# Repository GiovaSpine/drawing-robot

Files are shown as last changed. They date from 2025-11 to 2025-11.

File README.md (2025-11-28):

# Drawing Robot

This project is about a 3d printed **drawing robot** I made in my first year of computer engineering in 2023, to understand in more depth how a CNC machine works.  
It was 3D modeled in *FreeCAD* and programmed for an *Arduino Uno* entirely from scratch: from the classes that control the stepper motors, to the G-code functions that draw.

It was created before I started using proper version control, and I recently decided to publish it to share my work.

---

## The Robot

**The robot** is a SCARA manipulator with three degrees of freedom, that uses nema 17 stepper motors with GT2 belts and pulleys to reach a ratio of 20:1 for the first joint and 15:1 for the second joint.  
For the last joint we have a simple rack and pinion mechanism to convert the rotation of the stepper motor into a linear motion that moves the end effector (pen) to draw or not in the drawing plane.  

The code is divided in four *Arduino* files:
- [Scara_Manipulator_V1.ino](code/arduino/Scara_Manipulator_V1.ino): it's the main file where the classes for the stepper motors and the manipulator are declared, and the manipulator object is created.
- [CNCstepperClass.ino](code/arduino/CNCstepperClass.ino): where the class for the stepper motors is defined.
- [ManipulatorClass.ino](code/arduino/ManipulatorClass.ino): where the manipulator class is defined, with its functions that use the inverse kinematics to control the robot.
- [FunzioniGCODE.ino](code/arduino/FunzioniGCODE.ino): where the G-code functions of the manipulator class are defined.  

The following files allow to visualize the robot in 3D:
- *Blender* file (created with Blender 4.5): [Scara Manipulator.blend](3D-models/Scara%20Manipulator.blend)
- *.stl* file: [Scara Manipulator.stl](3D-models/pezzi/components/Scara%20Manipulator.stl)

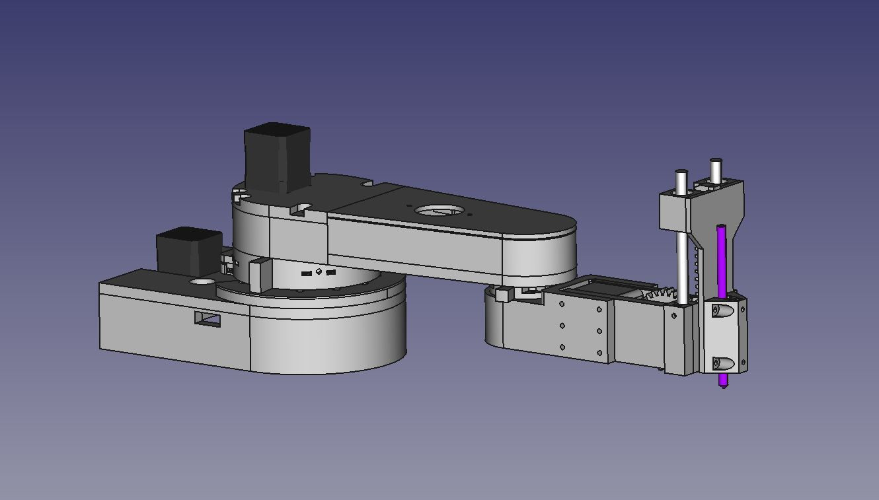
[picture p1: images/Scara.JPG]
Robot Frontale


---

## Robot in Action

The robot draws a butterfly.  

Robot in action 1

The robot draws a smiling face.  

Robot in action 3

The robot draws the letter "A".  

Robot in action 2

---

## Components
The robot was made in *FreeCAD* and designed to be able to be 3D printed in PLA with a cheap 3D printer.  
In addition we need the following components:

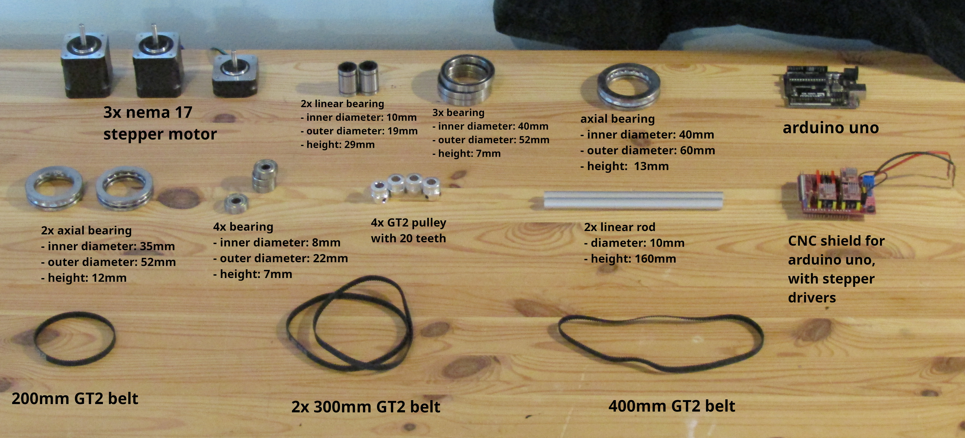
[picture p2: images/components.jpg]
Componenti Robot


---

## Robot Diagram
The robot has a very simple diagram, and in particular, since the objective is to draw, a complicated control for the $z$ axis is not needed, and so we can have two values for $z$: the value where the end effector (pen) is touching the drawing plane, and the value where it is not.  
As a result only the measurements for the horizontal links $d_2$ and $d_4$ are shown.

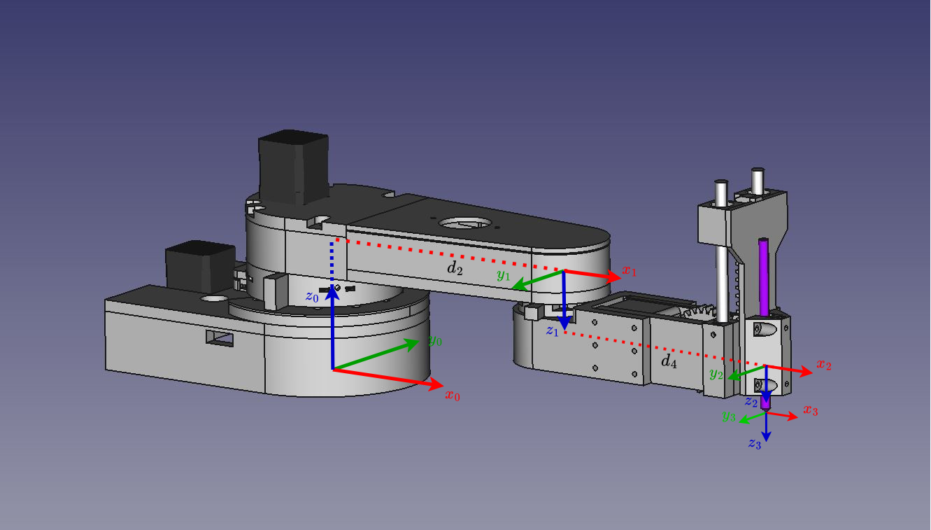
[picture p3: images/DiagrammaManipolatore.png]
Robot Diagram 1

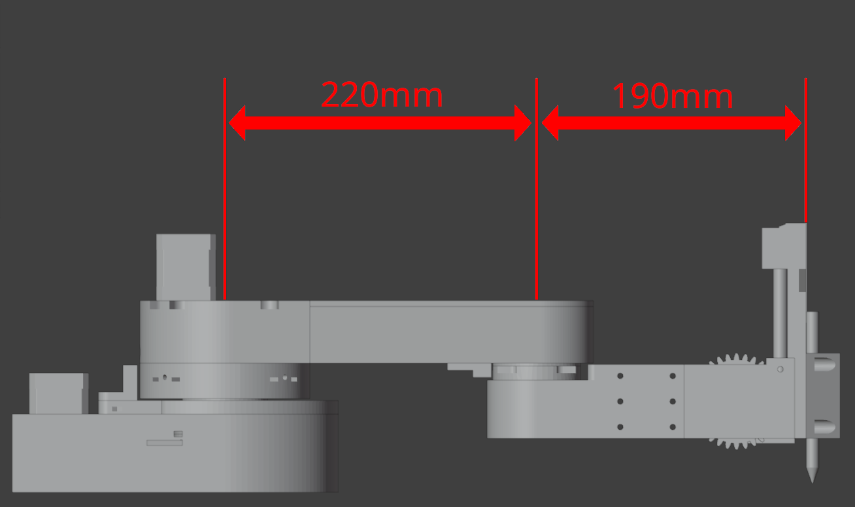
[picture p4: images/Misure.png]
Robot Diagram 2


---

## Inverse Kinematics
The **inverse kinematics** is very simple, not only because we have a three degrees of freedom manipulator, but also because with the simplification of the $z$ axis, discussed earlier, only $d_2$ and $d_4$ are used in the calculations for $\theta_1$ and $\theta_2$ (the angles of the first two joints respectively).  
For $\theta_3$ we need only to know the two values that allow the end effector (pen) to touch or not the drawing plane.

In the following image, two kinematic diagrams are shown. They represent a top view of the robot: one corresponds to a configuration where the desired $y_0$ is greater than 0, and the other where it is less than 0.
The equations derived using basic trigonometry are also included.
Inverse Kinematics

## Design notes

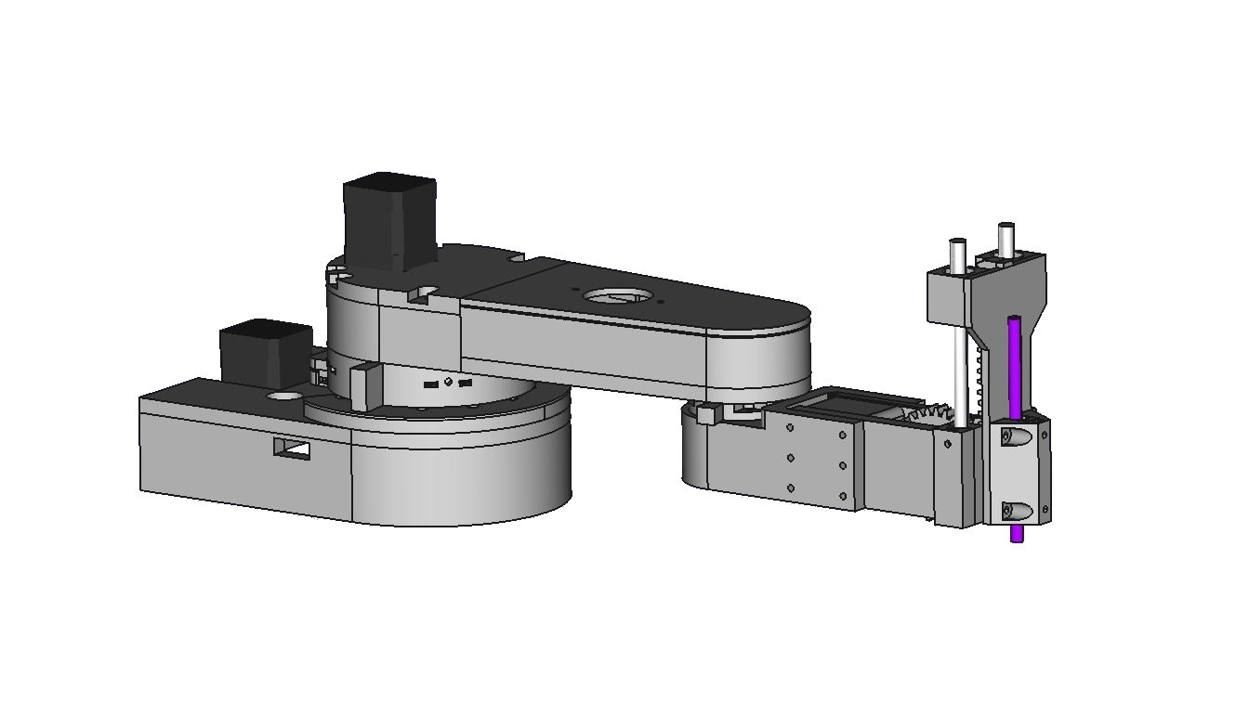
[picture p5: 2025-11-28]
images/Scara2.JPG

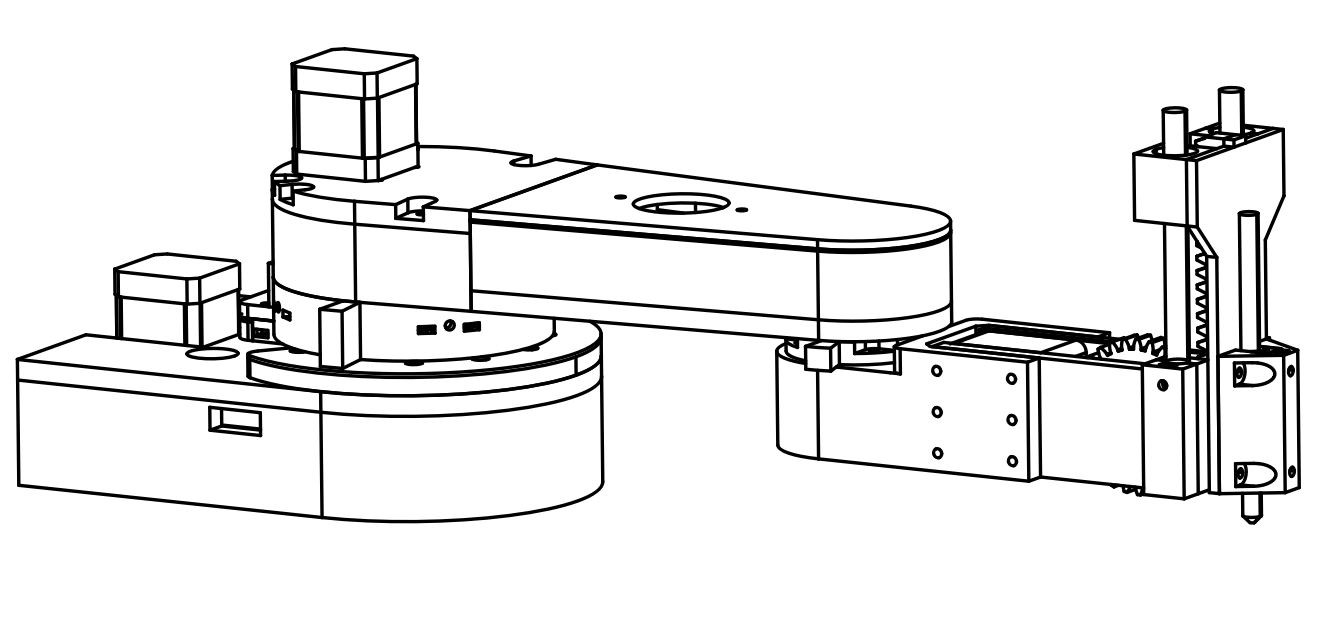
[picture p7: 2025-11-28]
images/Scara3.JPG

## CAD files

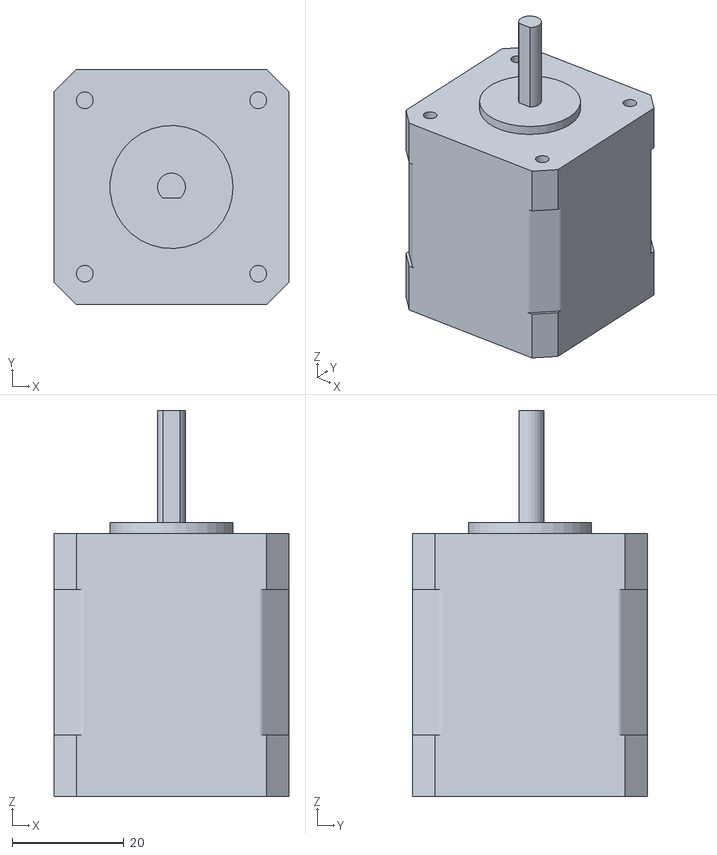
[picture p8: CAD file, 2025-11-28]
3D-models/pezzi/components/Stepper Motor-Nema 17 lenght_42.stl
42.0 x 42.0 x 69.0

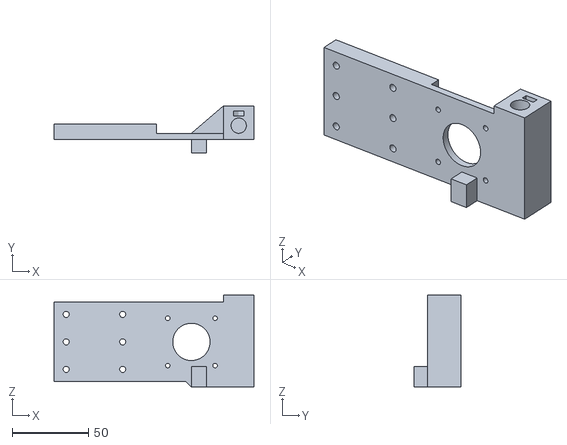
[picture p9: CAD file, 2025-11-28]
3D-models/pezzi/PJ-Base Pezzo Motore.stl
131.0 x 31.0 x 60.2

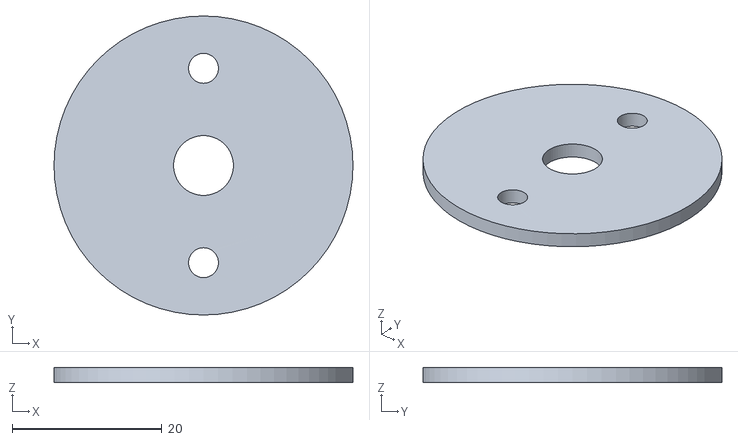
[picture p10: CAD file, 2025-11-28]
3D-models/pezzi/pulley/Coperchio Pulley 60 - Omero.stl
40.0 x 40.0 x 2.00

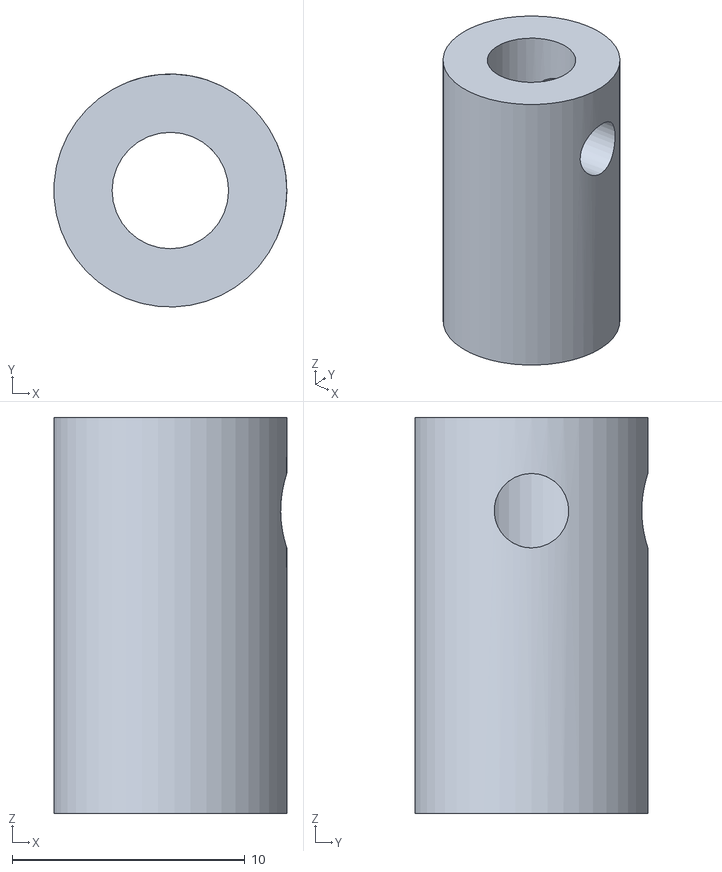
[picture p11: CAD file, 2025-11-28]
3D-models/pezzi/Albero Accopiamento Pulley-Nema 17.stl
9.99 x 10.00 x 17.0

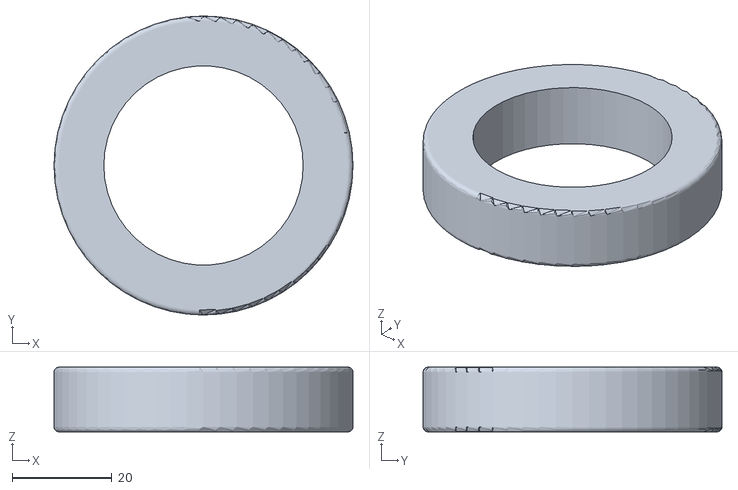
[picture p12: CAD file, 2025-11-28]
3D-models/pezzi/components/Cuscinetto assiale 40.stl
60.0 x 60.0 x 13.0

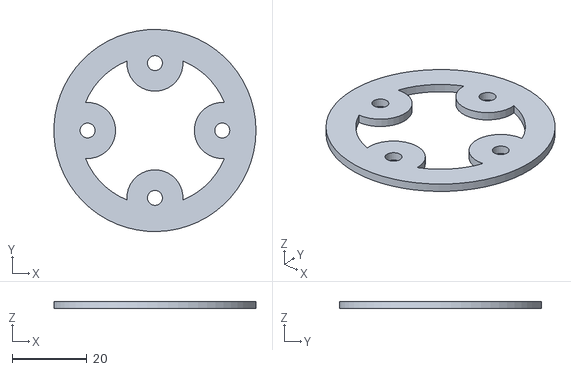
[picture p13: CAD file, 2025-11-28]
3D-models/pezzi/pulley/Coperchio Pulley 80 - Base.stl
54.0 x 54.0 x 2.00

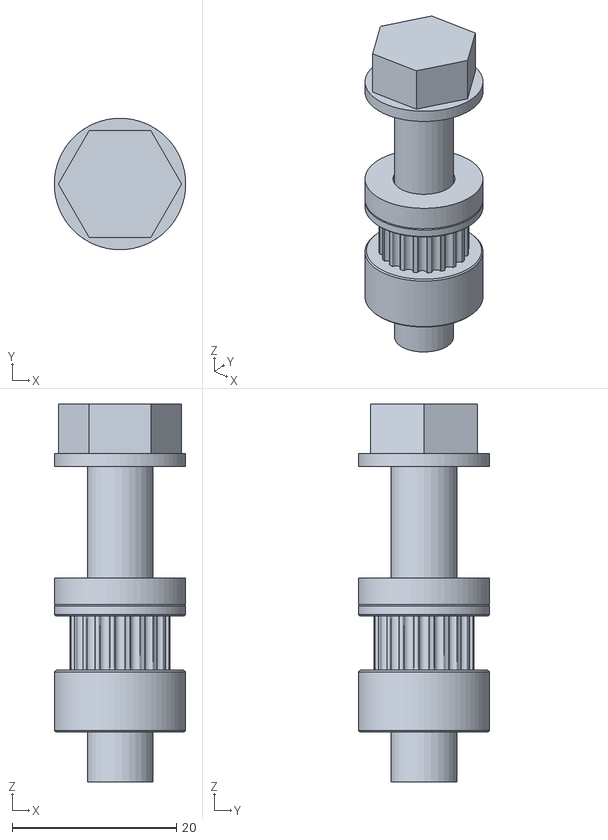
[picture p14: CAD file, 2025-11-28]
3D-models/pezzi/components/Oggetto.stl
16.0 x 16.0 x 46.0

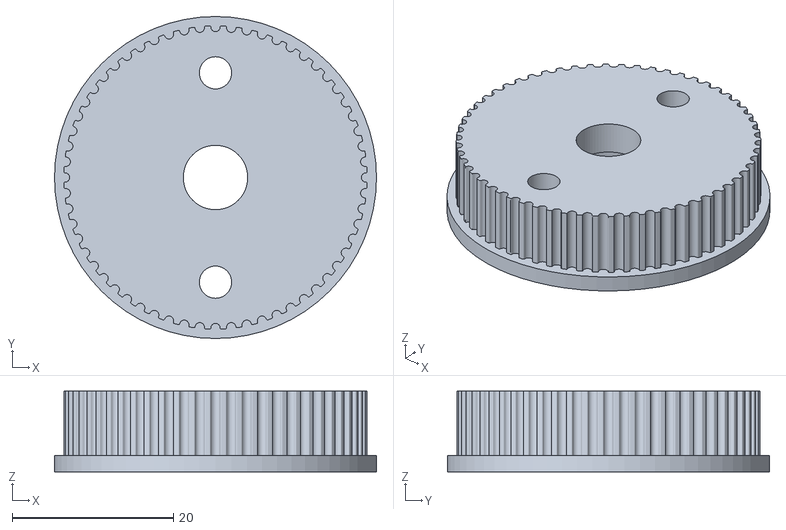
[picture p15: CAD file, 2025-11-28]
3D-models/pezzi/pulley/Pulley 60 - Omero.stl
40.0 x 40.0 x 10.0

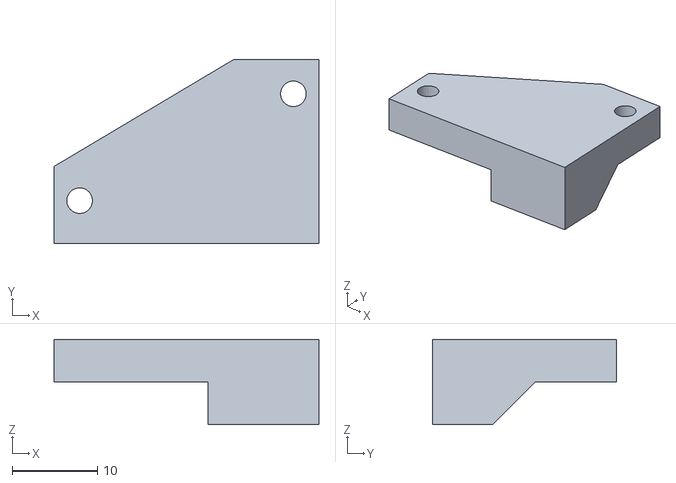
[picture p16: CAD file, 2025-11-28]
3D-models/pezzi/SCM-Test Micro Switch 2.stl
31.0 x 21.5 x 10.0

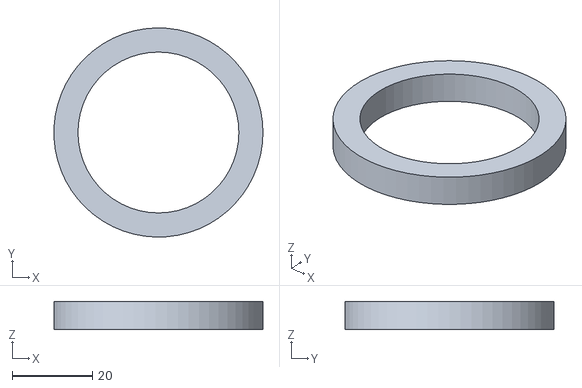
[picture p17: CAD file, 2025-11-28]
3D-models/pezzi/components/Cuscinetto radiale 40 2.stl
52.0 x 52.0 x 7.00

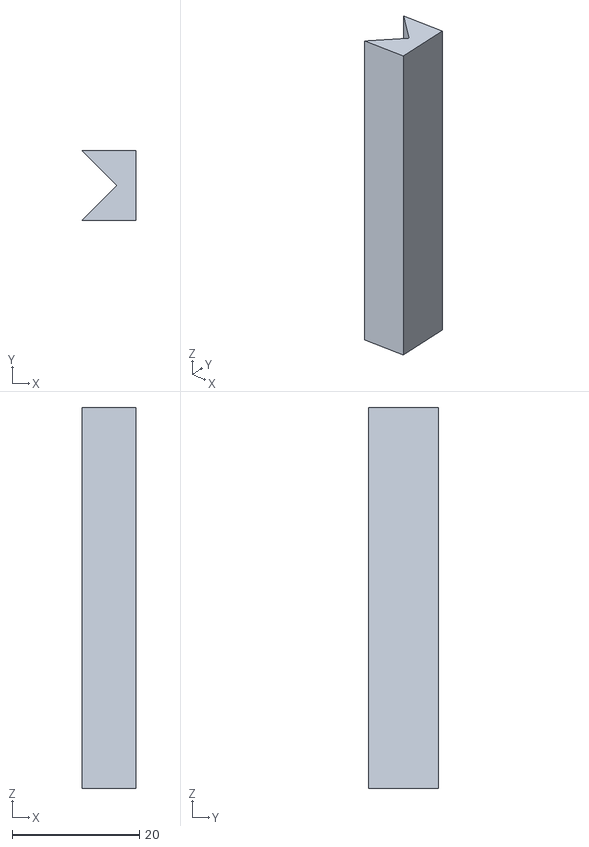
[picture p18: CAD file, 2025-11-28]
3D-models/pezzi/PJ-Pressa Penna.stl
8.50 x 11.0 x 60.0

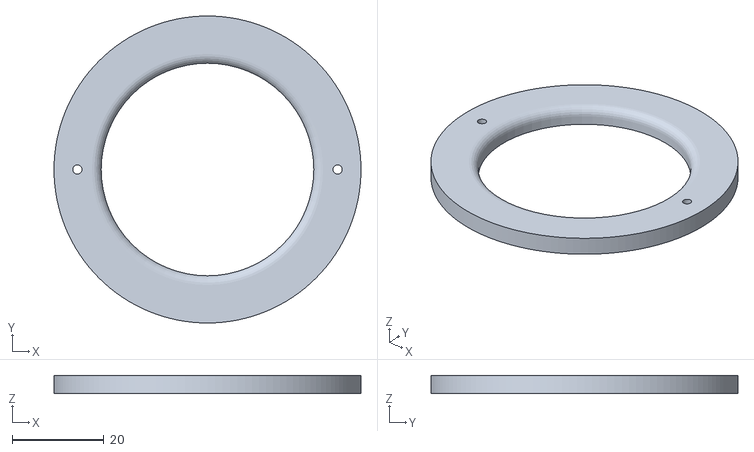
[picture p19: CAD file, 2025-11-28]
3D-models/pezzi/pulley/Coperchio Pulley 100 - Omero.stl
66.8 x 66.8 x 4.00

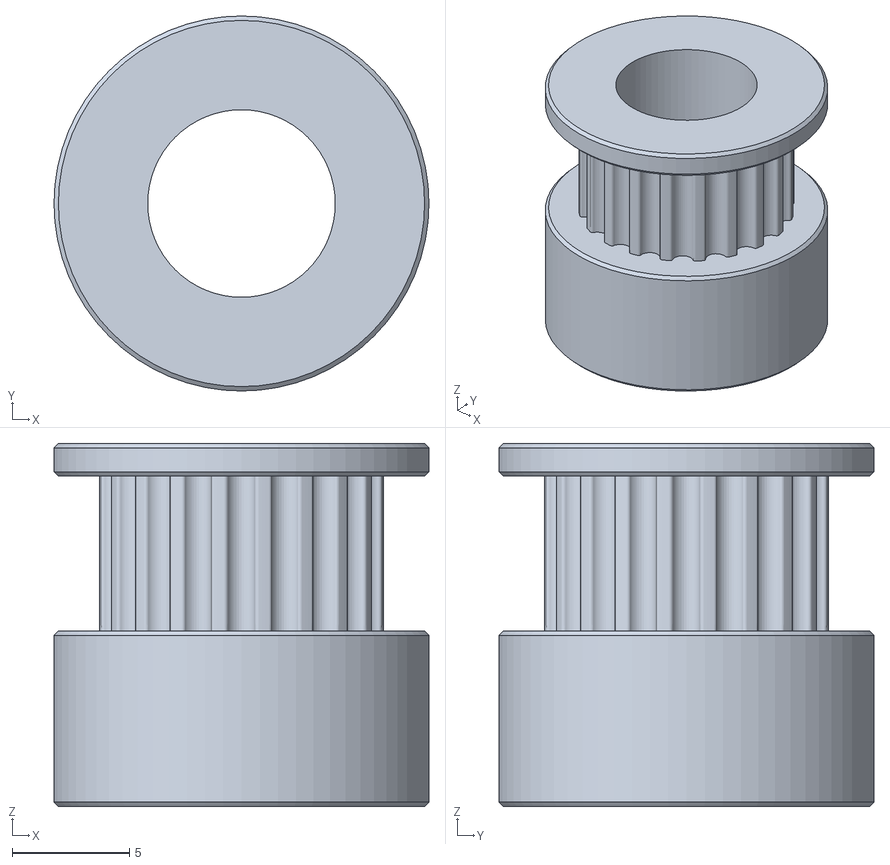
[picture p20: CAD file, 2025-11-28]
3D-models/pezzi/components/Pulley 20.stl
16.0 x 16.0 x 15.5

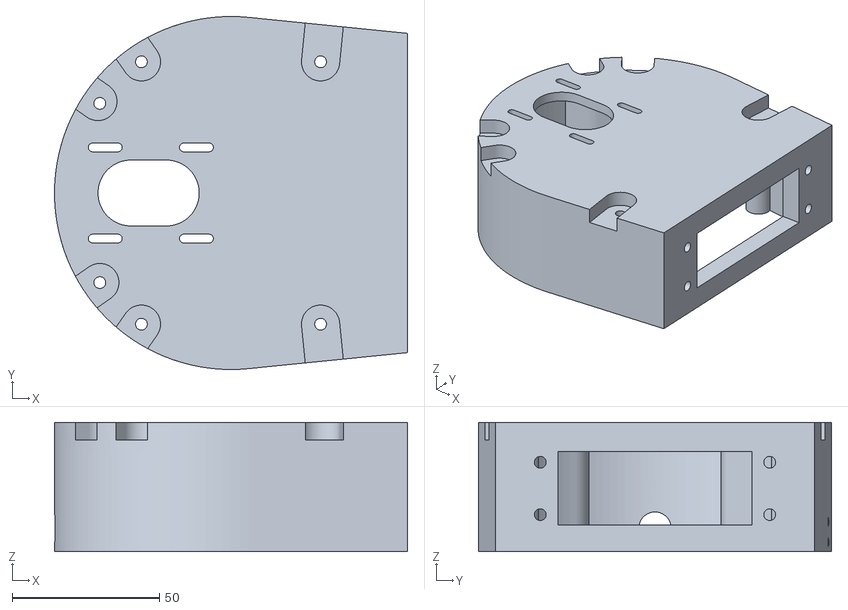
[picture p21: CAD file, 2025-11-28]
3D-models/pezzi/SCM-Omero Parte 1.stl
120.0 x 120.0 x 44.0

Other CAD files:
3D-models/pezzi/components/Cuscinetto assiale 35 2.stl
3D-models/pezzi/SCM-Rotore.stl
3D-models/pezzi/components/400mm GT2 Belt.stl
3D-models/pezzi/PJ-Involute Rack.stl
3D-models/pezzi/PJ-Base Pezzo 2.stl
3D-models/pezzi/PJ-Gear.stl
3D-models/pezzi/PJ-Pezzo Attacco Penna.stl
3D-models/pezzi/PJ-Ponte.stl
3D-models/pezzi/PJ-Radio.stl
3D-models/pezzi/SCM-Asse Gomito.stl
3D-models/pezzi/SCM-Asse Rotore 1.stl
3D-models/pezzi/SCM-Asse Rotore 2.stl
3D-models/pezzi/SCM-Base.stl
3D-models/pezzi/SCM-Coperchio Omero.stl
3D-models/pezzi/SCM-Coperchio Soffitto.stl
3D-models/pezzi/SCM-Gomito.stl
3D-models/pezzi/SCM-Omero Parte 2.stl
3D-models/pezzi/SCM-Soffitto Base.stl
3D-models/pezzi/components/200mm GT2 Belt.stl
3D-models/pezzi/components/300mm GT2 Belt 2.stl
3D-models/pezzi/components/300mm GT2 Belt.stl
3D-models/pezzi/components/Cuscinetto assiale 35.stl
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

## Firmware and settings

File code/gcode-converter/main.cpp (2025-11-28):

#include <iostream>
#include "gcode.h"

using namespace std;

int main() {
    //di norma è 140.0 105.0 per gli A4 verticali

    //dobbiamo convertire il GCODE generato con Inkscape
    //da un file di testo .txt in una serie di chiamate di funzioni C++
    //es. convertire "G03 X97.505069 Y259.737213 Z-1.000000 I0.047291 J-60.384406 F400.000000"
    //a "G03(363.237, 42.4949, -1, -60.3844, -0.047291);"

    //(ignoriamo le informazioni sulla velocià perché non dobbiamo tagliare/fresare)

    //come vediamo dall'esempio di sopra, non è una semplice conversione di testo ma c'è da applicare
    // un cambio di sistema di rifermento da sistema di riferimento del disegno a quello del robot

    //il vettore nel sistema di riferimento del robot, che punta verso il sistema di riferimento del foglio
    //è: (103.5, 140)
    //il sistema di riferimento del foglio deve avere (0, 0) in basso a sinistra (NON in alto a sinistra)

    double sdr_foglio_x = 103.5;
    double sdr_foglio_y = 140;
    gcode oggetto("disegni/Smile.ngc", sdr_foglio_x, sdr_foglio_y);
    oggetto.leggi();
    oggetto.scrivi();

    return 0;
}

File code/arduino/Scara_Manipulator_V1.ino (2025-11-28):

#include <math.h>
#define pi 3.141592


//in generale alcuni comandi gcode possono omettere X, Y o Z
//ciò significa che dobbiamo raggiungere un punto che ha le stesse coordinate di una delle x, y o z attuali
//"ASSENTE" è un valore che siamo sicuro non si può trovare nei comandi G, in quanto richiederebbe di avere una workspace molto grande
#define ASSENTE 100000.0


class Manipulator;


class CNCstepper {
private:
  int steps;  //steps correnti. Varia tra [0, 200*resolution*ratio]
  double ratio;

  double omega;  //velocità angolare con cui a prescindere ruota il joint
  double time;  //dipende da omega, è il delay in microsecondi da un passo all'altro

  double minAngle;  //vincolo MAX angolo raggiungibile <= 360
  double maxAngle;  //vincolo min angolo raggiungibile >= -360

  int stepPin;  //pin dei motori, derivano da dove si collega il motore allo shield (X, Y o Z)
  int dirPin;  //direzione "dir" indica in quale verso deve ruotare (orario (HIGH) o antiorario (LOW))
  
  double resolution;  //risoluzione degli step, di default è 1, quindi 1.8 gradi per step. Può valere 1, 2, 4, 8, 16

private:
  double funzione_tempo(double x, double steps, double time0, double percentuale = 20.0, double ritardo = 2.0);

public:
  CNCstepper(char identificatore, double velocita, int ratio, int resolution = 1);

  void inizializza();
  void set_vincolo(double min, double max);

  int steps_value();
  int ratio_value();

  void angle_iter(double angle);
  void angle_iter_acc(double angle, double percentuale = 20.0, double ritardo = 2.0);
  void angle_configure(double angle, double percentuale = 20.0, double ritardo = 2.0);

  friend class Manipulator;
};


class Manipulator{
private:
  const double raggioEndEffector;

  CNCstepper joint1;
  CNCstepper joint2;
  CNCstepper joint3;

  double theta1;
  double theta2;
  double theta3;
  
  double current_x;
  double current_y;
  bool current_z;

private:
  void trigonometriaV1(double x, double y);
  double norma(double x, double y);

  void alza_EF();
  void abbassa_EF();
    
  void raggiungi_punto_iter(double x, double y, bool z);

  //codici gcode
  void G00(double X, double Y, double Z);
  void G01(double X, double Y, double Z);
  void G02(double X, double Y, double Z, double I, double J);
  void G03(double X, double Y, double Z, double I, double J);

public:
  Manipulator(double raggio_EndEffector);
  void inizializza();

  void home();

  void raggiungi_punto(double x, double y);
  void punto();
  void segmento(double x, double y);

  void Draw();
};

//======================================================================================================================================================

//inizializziamo il manipolatore con il raggio del pennarello
//perché impatta nella distanza del link e quindi nella trigonometria
Manipulator Scara(8.33/2.0);




void setup() {
  Serial.begin(9600);

  delay(5000);

  Scara.inizializza();
}



void loop() {

  Serial.println("Test");


  delay(2000);
  Scara.Draw();

  Scara.home();  
}

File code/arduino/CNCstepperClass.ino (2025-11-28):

//COSTRUTTORE
CNCstepper::CNCstepper(char iden, double velocita, int ratio, int res){
    
  this->steps = 0;

  //----------------------------------------
  //ratio
  this->ratio = double(ratio);

  //----------------------------------------
  //tali numeri derivano dal tipo di Shield
  if(iden == 'X' || iden == 'x') {stepPin = 2; dirPin = 5;}
  if(iden == 'Y' || iden == 'y') {stepPin = 3; dirPin = 6;}
  if(iden == 'Z' || iden == 'z') {stepPin = 4; dirPin = 7;}

  //----------------------------------------

  this->omega = velocita;  //velocita angolare, es. 360 gradi/s
  double Periodo = ((360.0) / omega) * 1000000.0;  //Periodo T in microsecondi  (T = 2pi / w)
  this->time = Periodo / (400.0 * this->ratio);  //tempo in microsecondi tra un impulso e l'altro
  
  //sanificazione di velocita
  if(this->time <= 600.0){  //perde passi (funziona male) per delay minori a 600
    Serial.begin(9600);
    while(true) {Serial.print("->Errore: velocità angolare non raggiungibile, time =  "); Serial.print(time); Serial.println(" <= 600 !");}
  }

  //----------------------------------------
  //di default il motore (considerabile come un servomotore) può raggiungere un angolo appartenente a [-360, 360]
  this->minAngle = -360.0;
  this->maxAngle = 360.0;
  
  //----------------------------------------
  //resolution è un valore reale per cercare di evitare perdità di precisone
  if(res != 1 && res != 2 && res != 4 && res != 8 && res != 16){
    Serial.begin(9600);
    while(true) Serial.println("->Errore: risoluzione non valida");
  }
  else this->resolution = double(res);
  
}

//===================================================================================================================================

void CNCstepper::inizializza(){
  //-->funzione che:
  //setta come output i pin opportuni. DA INVOCARE nel setup
  pinMode(stepPin, OUTPUT);
  pinMode(dirPin, OUTPUT);
}


//===================================================================================================================================

void CNCstepper::set_vincolo(double min, double max){
  if(min < -360.0 || min >= 360.0){
    Serial.begin(9600);
    while(true) Serial.print("->Errore: vincolo non valido");
  }

  if(max <= -360.0 || max > 360.0){
    Serial.begin(9600);
    while(true) Serial.print("->Errore: vincolo non valido");
  }

  this->minAngle = min;
  this->maxAngle = max;
}
//===================================================================================================================================

void CNCstepper::angle_iter(double angle){
  //-->funzione che:
  //blocca l'esecuzione del programma: fino a quando l'angolo non è raggiunto non verrà eseguito nessun altro codice

  if(angle < minAngle) angle = minAngle;
  if(angle > maxAngle) angle = maxAngle;

  //proporzione per ottenere gli steps che corrispondono all'angolo desiderato
  //int angle_steps = int( (angle * 20.0 * resolution / 36.0 );
  int angle_steps = int(  double(angle) / double( 36.0 / (20.0 * resolution * this->ratio) )  );
  
  if(angle_steps == this->steps){
    //angolo raggiunto
    return;
  }

  int local_steps = 0;  //steps da fare per raggiungere l'angolo

  if(this->steps < angle_steps){
    digitalWrite(dirPin, LOW);  //deve girare in senso antiorario per raggiungerlo
    local_steps = angle_steps - this->steps;
  }

  if(this->steps > angle_steps){
    digitalWrite(dirPin, HIGH);  //deve girare in senso orario per raggiungerlo
    local_steps = this->steps - angle_steps;
  }

  //importante questo
  this->steps = angle_steps;
  
  for(int i=0;  i < (local_steps);  i++){    
    digitalWrite(stepPin, HIGH); 
    delayMicroseconds(time);
    digitalWrite(stepPin, LOW); 
    delayMicroseconds(time);    
  }

  //ritardo per non far partire subito gli altri motori
  //delay(1500);
  delayMicroseconds(time);
}

//===================================================================================================================================

void CNCstepper::angle_configure(double angle, double percentuale, double ritardo){
  //-->funzione che:
  //raggiunge l'angolo desiderato, bloccando il programma, in quanto si ha un for
  //non viene però modificato il membro privato "steps"
  //per cui ruota il motore di "angle" a prescindere se rispetto ad un sistema di riferimento

  //proporzione per ottenere gli steps che corrispondono all'angolo desiderato
  //int angle_steps = int( (angle * 20.0 * resolution) / 36.0 );
  int angle_steps = int(  double(angle) / double( 36.0 / (20.0 * resolution * this->ratio) )  );
  
  if(angle_steps == this->steps){
    //angolo raggiunto
    return;
  }

  int local_steps = 0;  //steps da fare per raggiungere l'angolo

  if(this->steps < angle_steps){
    digitalWrite(dirPin, LOW);  //deve girare in senso antiorario per raggiungerlo
    local_steps = angle_steps - this->steps;
  }

  if(this->steps > angle_steps){
    digitalWrite(dirPin, HIGH);  //deve girare in senso orario per raggiungerlo
    local_steps = this->steps - angle_steps;
  }

  for(int i=0;  i < (local_steps);  i++){
    double tempo = funzione_tempo(i, local_steps, time, percentuale, ritardo);
    digitalWrite(stepPin, HIGH); 
    delayMicroseconds(tempo);
    digitalWrite(stepPin, LOW); 
    delayMicroseconds(tempo);    
  }

  //ritardo per non far partire subito gli altri motori
  delay(1000);
}

//===================================================================================================================================

double CNCstepper::funzione_tempo(double x, double steps, double time0, double percentuale, double ritardo){
  //-- x è a che passo è tra [0, steps]
  //-- calcola un ritardo per avere una rotazione accelerata e decelerata
  //-- suppondendo percentuale sia pari a 20%, ciò significa che verrà calcolato un ritardo che cala progressivamente fino alla velocità ordinaria
  //   per il primo 20% della rotazione e l'ultimo 80%
  //-- l'utente può inserire quanto ritardare, tipo ritardo = 2, allora il max ritardo sarà 2*time

  //ATTENZIONE: si può rendere piu efficiente, evitando di calcolare p1 e p2 ogni volta !

  if(percentuale <= 0.0 || percentuale > 50.0){
    Serial.begin(9600);
    while(true) Serial.println("->Errore: funzione_tempo");
  }
  if(ritardo < 1.0 || ritardo > 10.0){
    Serial.begin(9600);
    while(true) Serial.println("->Errore: funzione_tempo");
  }

  //double p1 = (  (4.0 * steps * steps)  /  ( ((25.0 * ritardo) - 25.0)*time0 )  );
  double p1 = -1.0 * (   ( ((percentuale*percentuale) - (100.0*percentuale))*(steps*steps) )  /  ((10000.0*ritardo - 10000.0) * time0)    );
  double p2 = (ritardo * time0) - ( (steps*steps) / (4.0*p1) );

  double tempo = (( (x - (steps/2.0))*(x - (steps/2.0)) ) / p1) + p2;  //la y nella funzione

  if(tempo <= time0) return time0;
  else return tempo;
}
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

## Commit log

2025-11-28 Remove not useful 3d models. Implement README.md
    [Scara Manipulator No_1 - mini-Componenti interne Basedistanza 47mm.stl, Scara Manipulator No_1 - mini-Componenti interne Basedistanza 88mm.stl, Scara Manipulat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]
2025-11-28 Add complete 3d model of the robot as stl file. Improve README.md
